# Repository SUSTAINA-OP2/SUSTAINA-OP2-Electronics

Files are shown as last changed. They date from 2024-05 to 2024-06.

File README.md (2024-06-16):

<h1 align="center">
    Printed Circuit Boards for SUSTAINA-OP2&trade;
</h1>
<table align="center">
    <tr>
        <td align="center"><a href="./SUSTAINA-Constant-Voltage-Board">Constant Voltage Board</a></td>
        <td align="center"><a href="./SUTAINA-Control-Switches-Board">Control Switches Board</a></td>
        <td align="center"><a href="./SUSTAINA-PMX-Control-Board">PMX Control Board</a></td>
    </tr>
    <tr>
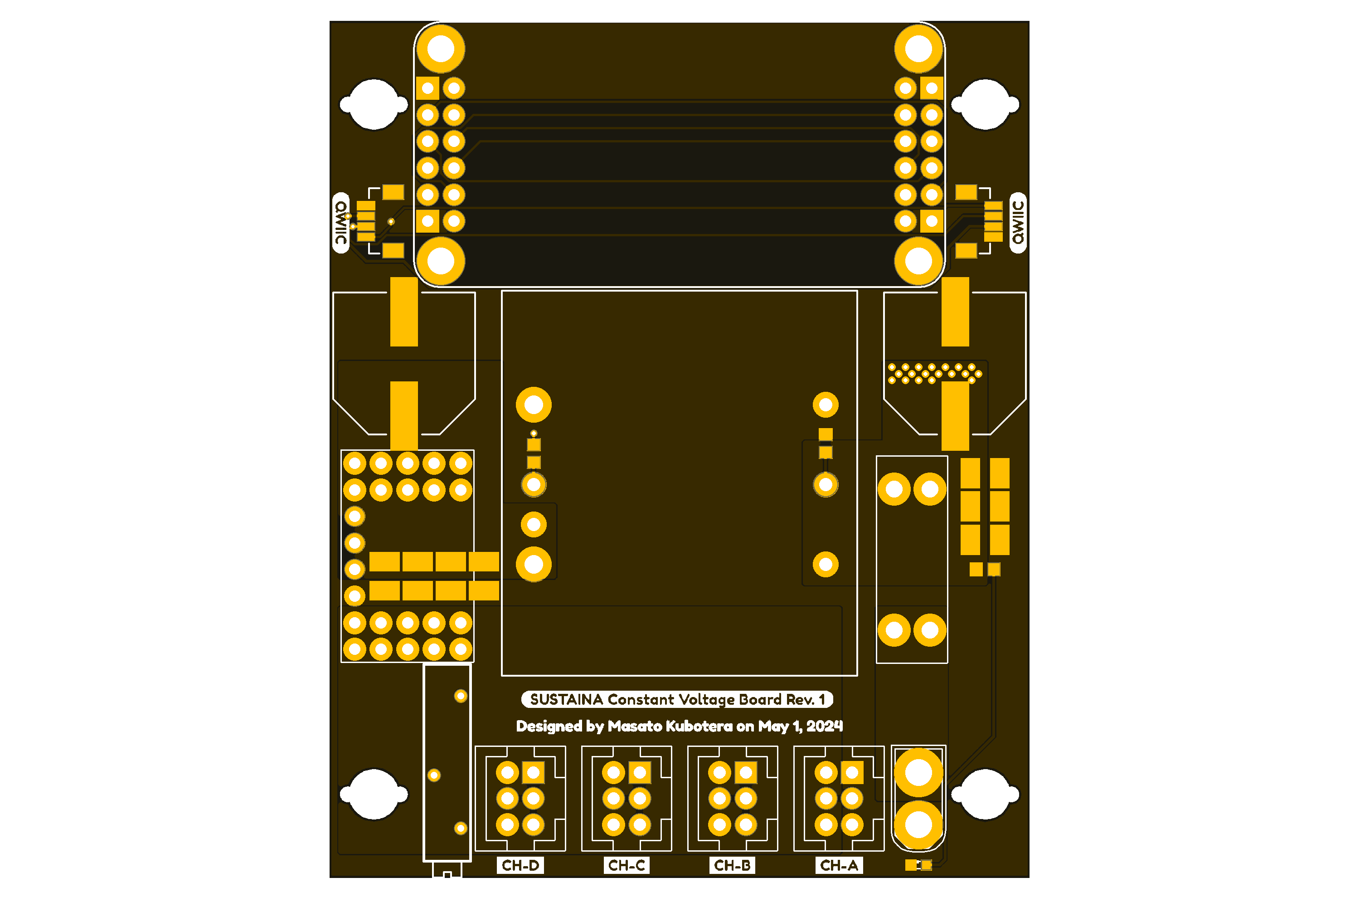
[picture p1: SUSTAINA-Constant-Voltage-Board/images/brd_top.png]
        <td align="center"></td>
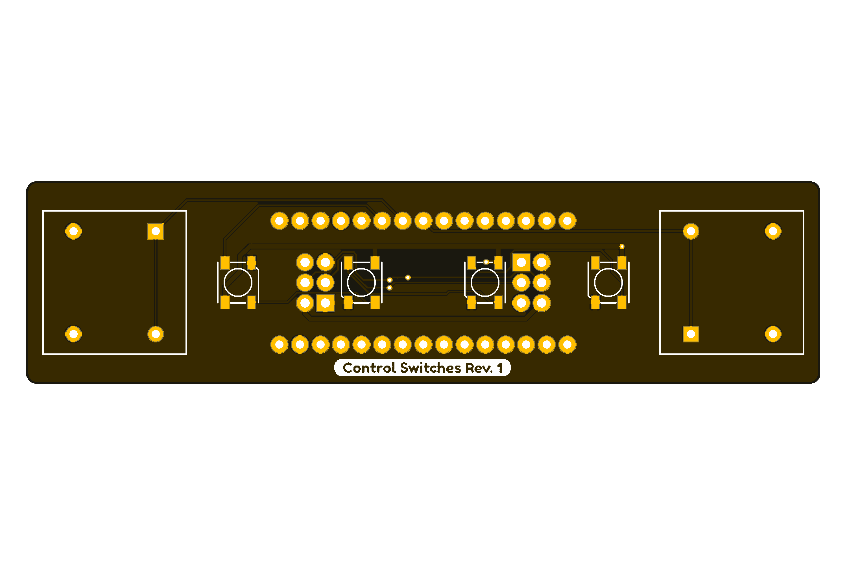
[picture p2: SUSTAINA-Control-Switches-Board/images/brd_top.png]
        <td align="center"></td>
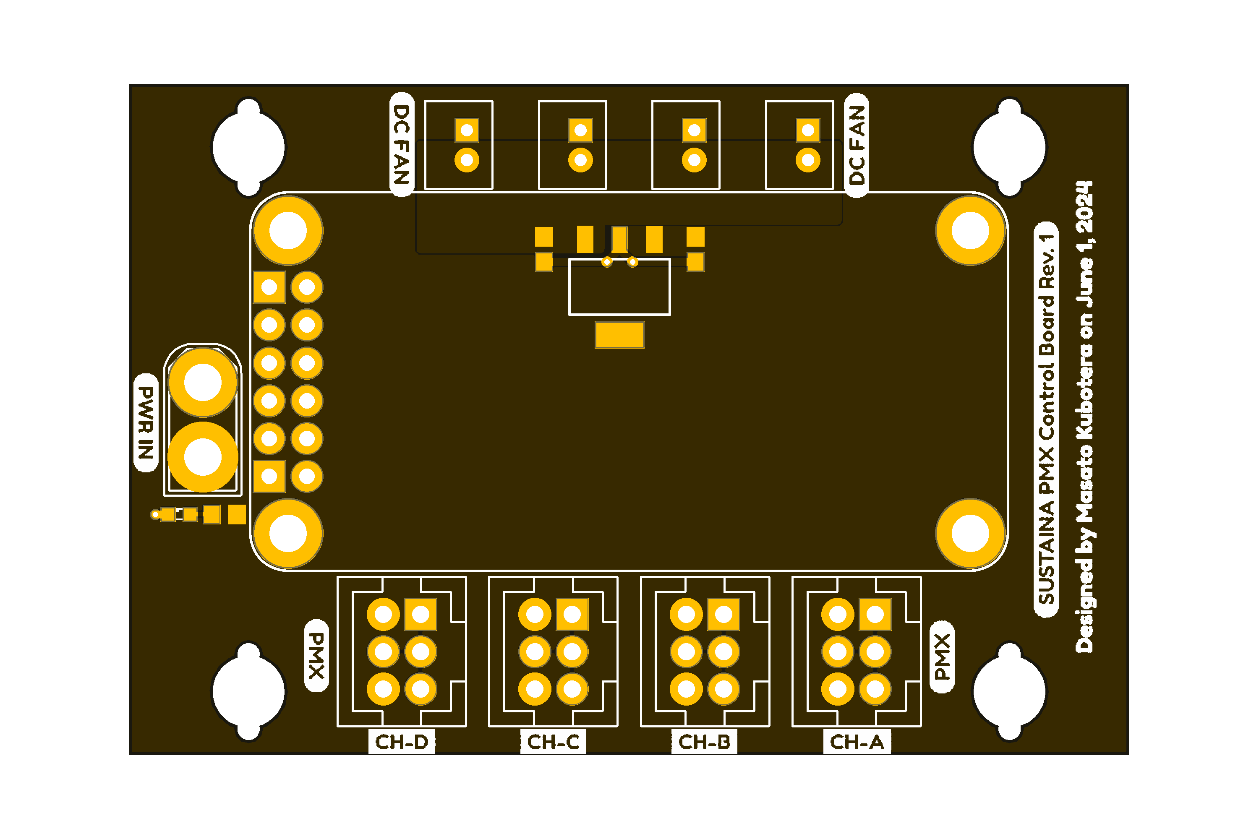
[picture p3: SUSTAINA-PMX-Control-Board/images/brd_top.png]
        <td align="center"></td>
    </tr>
    <tr>
        <td align="center"><a href="./SUSTAINA-Power-Logging-Board">Power Logging Board</a></td>
        <td align="center"><a href="./SUSTAINA-Power-Distribution-Board">Power Distribution Board</a></td>
        <td align="center"><a href="./SUSTAINA-Power-Supply-Switching-Board">Power Supply Switching Board</a></td>
    </tr>
    <tr>
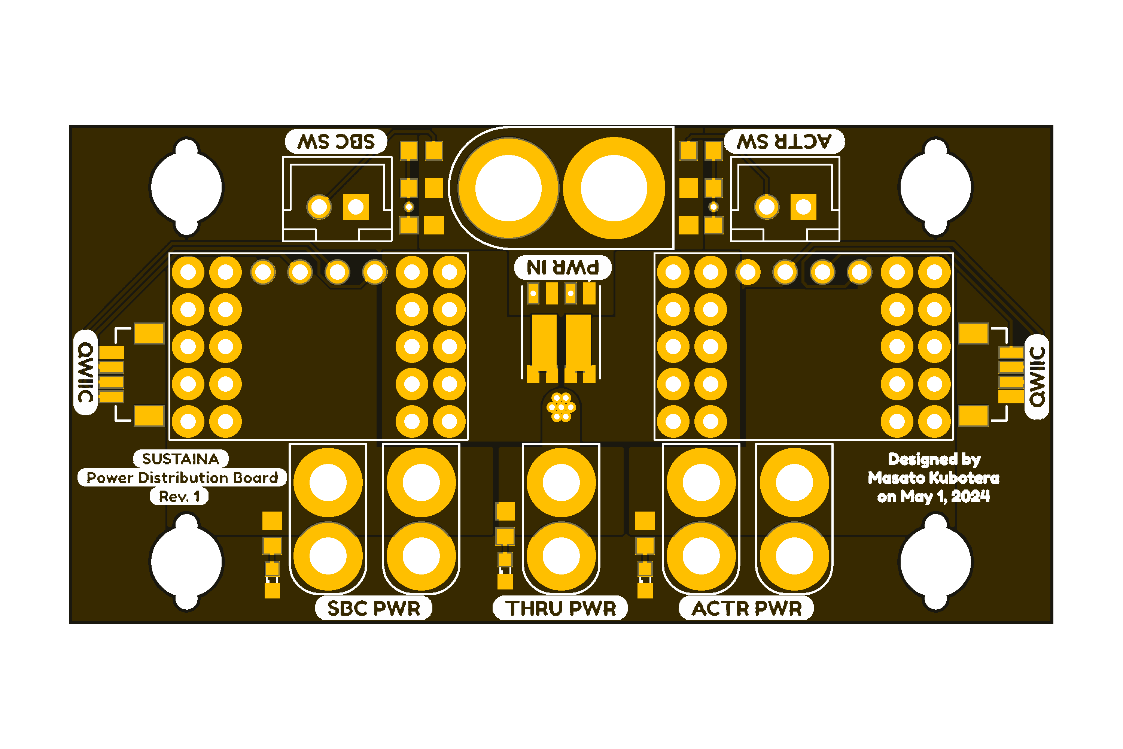
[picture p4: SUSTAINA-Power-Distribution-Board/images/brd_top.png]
        <td align="center"></td>
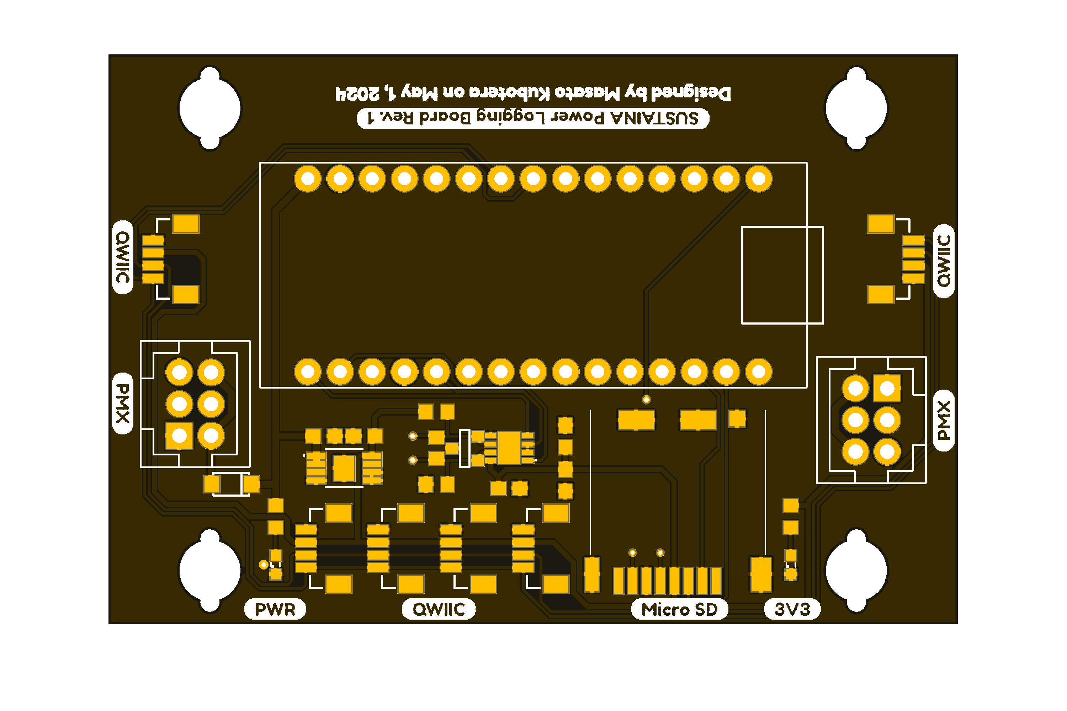
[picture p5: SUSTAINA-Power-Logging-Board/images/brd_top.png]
        <td align="center"></td>
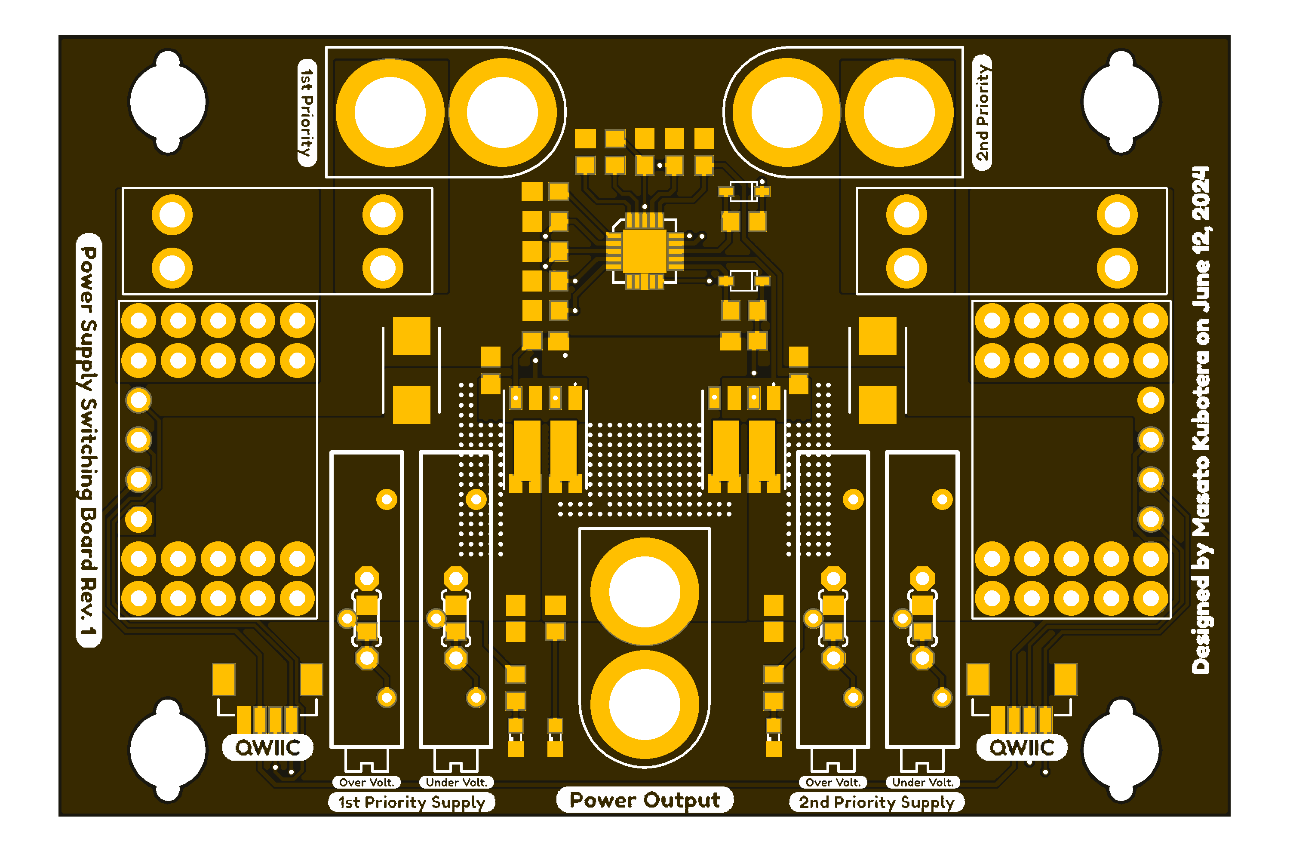
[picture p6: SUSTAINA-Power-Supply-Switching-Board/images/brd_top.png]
        <td align="center"></td>
    </tr>
    <tr>
        <td align="center"><a href="./SUSTAINA-SBC-Power-Board">SBC Power Board</a></td>
        <td align="center"><a href="./SUSTAINA-SCI-Extension-Board">SCI Extension Board</a></td>
        <td align="center"><a href="./SUSTAINA-StrainGauge-Sensing-Board">Strain Gauge Sensing Board</a></td>
    </tr>
    <tr>
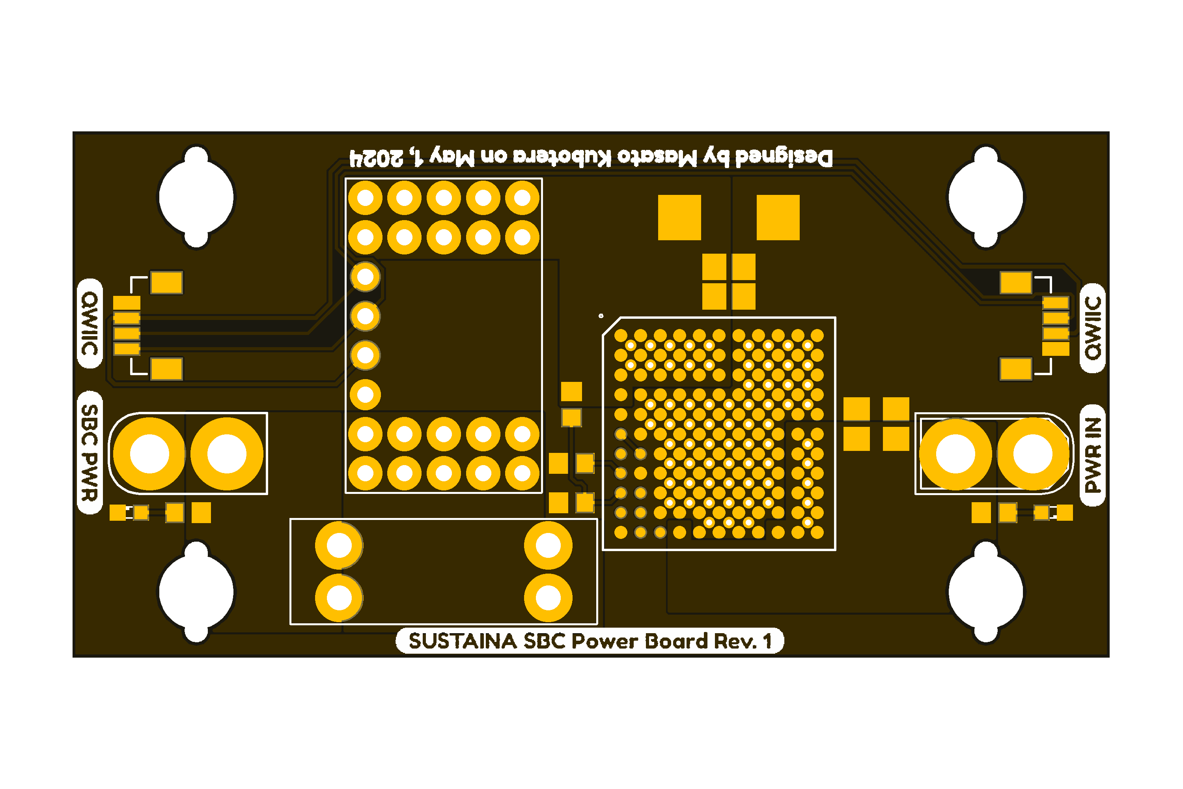
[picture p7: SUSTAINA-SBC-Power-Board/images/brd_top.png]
        <td align="center"></td>
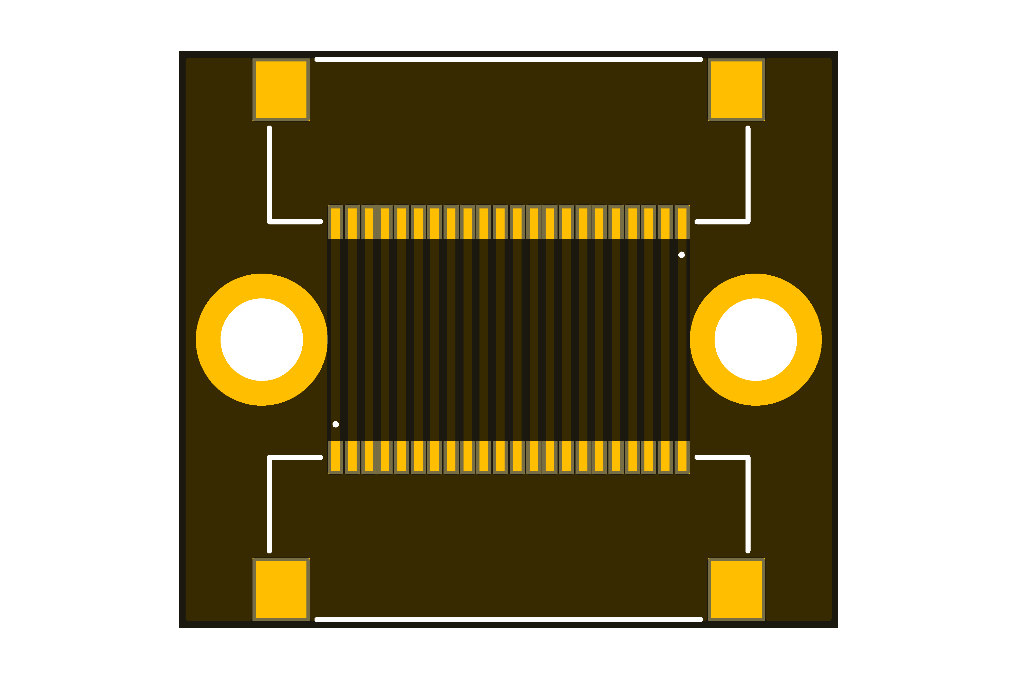
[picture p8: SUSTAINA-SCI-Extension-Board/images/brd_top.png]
        <td align="center"></td>
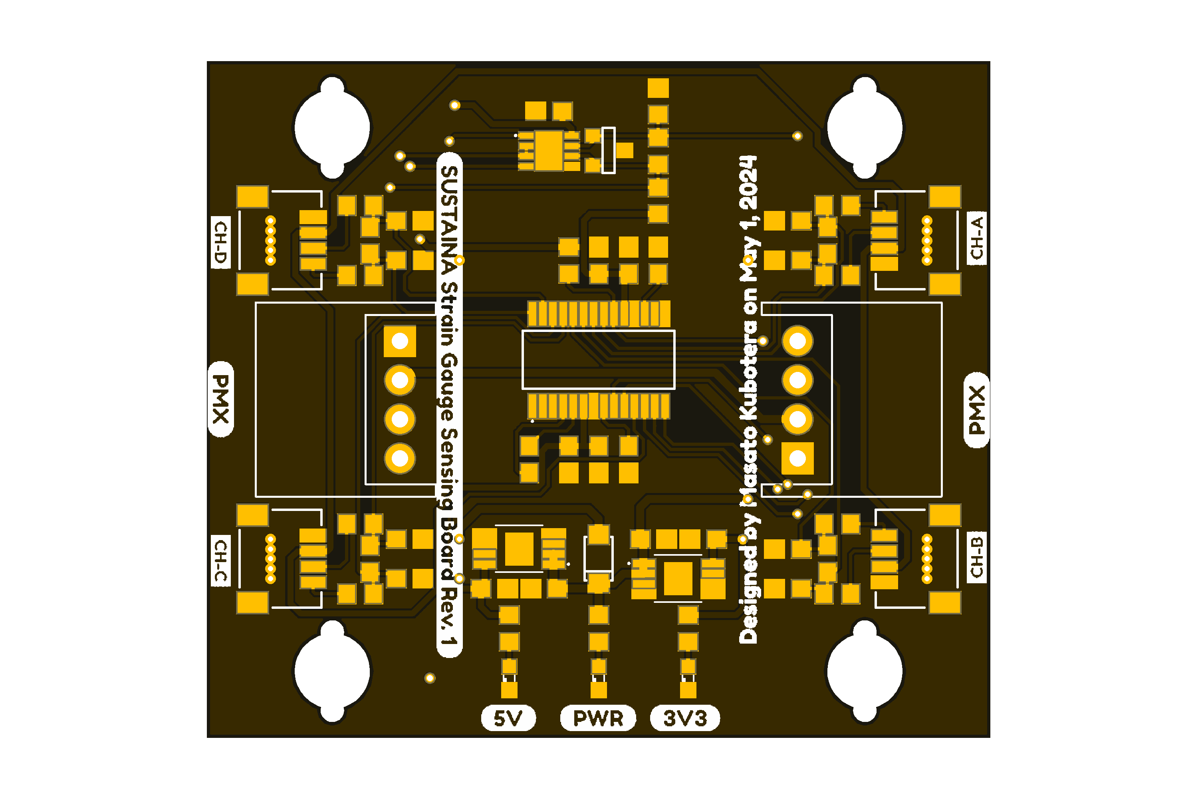
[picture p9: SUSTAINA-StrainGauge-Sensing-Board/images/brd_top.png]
        <td align="center"></td>
    </tr>
    <tr>
        <td align="center"><a href="./SUSTAINA-Power-Monitor-Module">Power Monitor Module</a></td>
        <td align="center"><a href="./SUSTAINA-USB-to-Quad-RS-485-Conv-Module">USB to Quad RS-485 Conv. Module</a></td>
        <td align="center"></td>
    </tr>
    <tr>
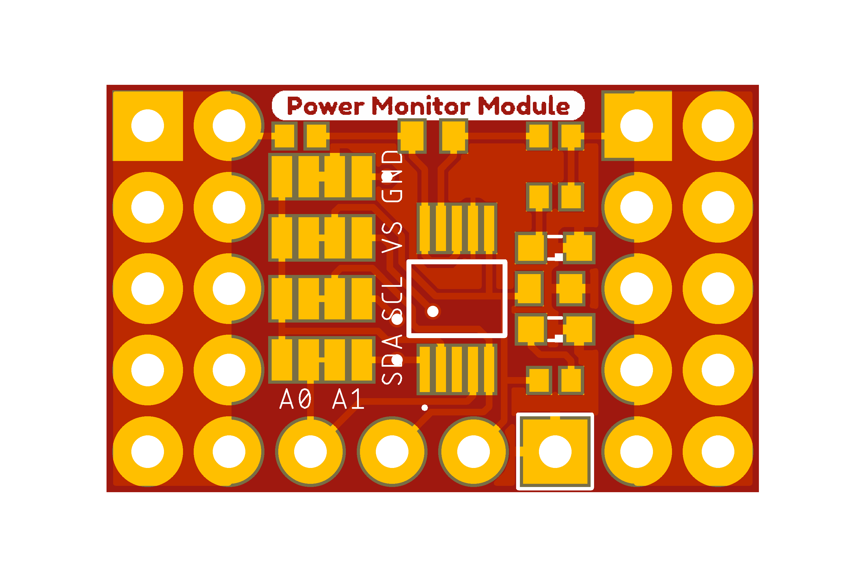
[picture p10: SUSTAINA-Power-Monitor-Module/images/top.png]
        <td align="center"></td>
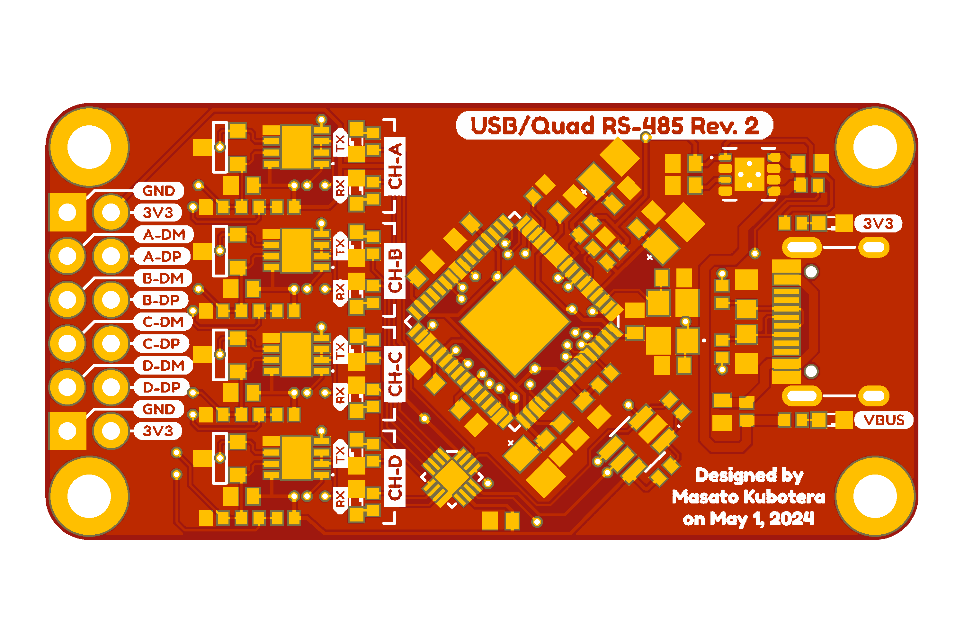
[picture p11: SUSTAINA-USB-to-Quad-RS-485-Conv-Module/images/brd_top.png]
        <td align="center"></td>
        <td align="center"></td>
    </tr>
</table>

> [!NOTE]
> This repository provides design and order data for PCBs of SUSTAINA-OP2&trade;.<br>
> Other SUSTAINA-OP2&trade; contents
> - Mechanical: https://github.com/SUSTAINA-OP/SUSTAINA-OP2
> - Firmware: https://github.com/SUSTAINA-OP/SUSTAINA-OP2-Firmware

## Features of SUSTAINA-OP2&trade;'s PCBs

All PCBs for SUSTAINA-OP are compatible with PCBA, which can reduce production barriers (such as selecting and assembling electronic components) before they are assembled into robots.

The PCB fabrication and PCBA used for all SUSTAINA-OP2 are outsourced to JLCPCB!

> [!WARNING]
> Some components to be assembled on the PCB (e.g. not in stock or not handled)  cannot be assembled using PCBA and must be assembled by yourself.

## Repository Contents

The PCBs of SUSTAINA-OP2&trade; can be divided into two main categories.<br>
The first is "module," which packages sensors, conversion circuits, etc. in functional units on a single board and can be easily replaced.<br>
The second is "board", which is a multifunctional PCB with modules and other components.

### Boards
- [Constant Voltage Board](./SUSTAINA-Constant-Voltage-Board)
- [Control Switches Board](./SUTAINA-Control-Switches-Board)
- [PMX Control Board](./SUSTAINA-PMX-Control-Board)
- [Power Logging Board](./SUSTAINA-Power-Logging-Board)
- [Power Distribution Board](./SUSTAINA-Power-Distribution-Board)
- [Power Supply Switching Board](./SUSTAINA-Power-Supply-Switching-Board)
- [SBC Power Board](./SUSTAINA-SBC-Power-Board)
- [SCI Extension Board](./SUSTAINA-SCI-Extension-Board)
- [StrainGauge Sensing Board](./SUSTAINA-StrainGauge-Sensing-Board)

### Modules
- [Power Monitor Module](./SUSTAINA-Power-Monitor-Module)
- [USB to Quad RS-485 Conv. Module](./SUSTAINA-USB-to-Quad-RS-485-Conv-Module)

## Development Environment
The PCBs for SUSTAINA-OP2&trade; were designed in **Autodesk Eagle 9.6.2**.

## License Information
This product is open source. Please review the [LICENSE(EN)](/LICENSE) / [LICENSE(JA)](/LICENSE-JA) for license information.

This product by Masato Kubotera is licensed under a [CC BY-NC-SA 4.0 DEED](http://creativecommons.org/licenses/by-nc-sa/4.0/).

> [!NOTE]
> **Summary:**
> - **Attribution** — You must give appropriate credit , provide a link to the license, and indicate if changes were made.
> - **NonCommercial** — You may not use the material for commercial purposes.
> - **ShareAlike** — If you remix, transform, or build upon the material, you must distribute your contributions under the same license as the original.

> [!TIP]
> - **Examples of appropriate credit** — [SUSTAINA-OP2&trade;](https://github.com/SUSTAINA-OP/SUSTAINA-OP) &copy; Masato Kubotera (2024) CC BY-NC-SA 4.0 DEED
> >
> - **Reference & Citation**  
>   To reference and/or cite the work contained in this repository, please use the following publications:
>   - Kubotera, M. and Hayashibara, Y.: SUSTAINA-OP&trade;: Kid-sized Open Hardware Platform Humanoid Robot with Emphasis on Sustainability. RoboCup 2023: Robot World Cup XXVI, pp.166–178 (2024) [Springer](https://link.springer.com/chapter/10.1007/978-3-031-55015-7_14)
>
>     **The paper is about SUSTAINA-OP&trade;. Publications on SUSTAINA-OP2&trade; will be published soon.**

## Contact
If you have any questions, please contact the designer of this product, Masato Kubodera, by [E-mail](masatokubotera06@yahoo.co.jp).

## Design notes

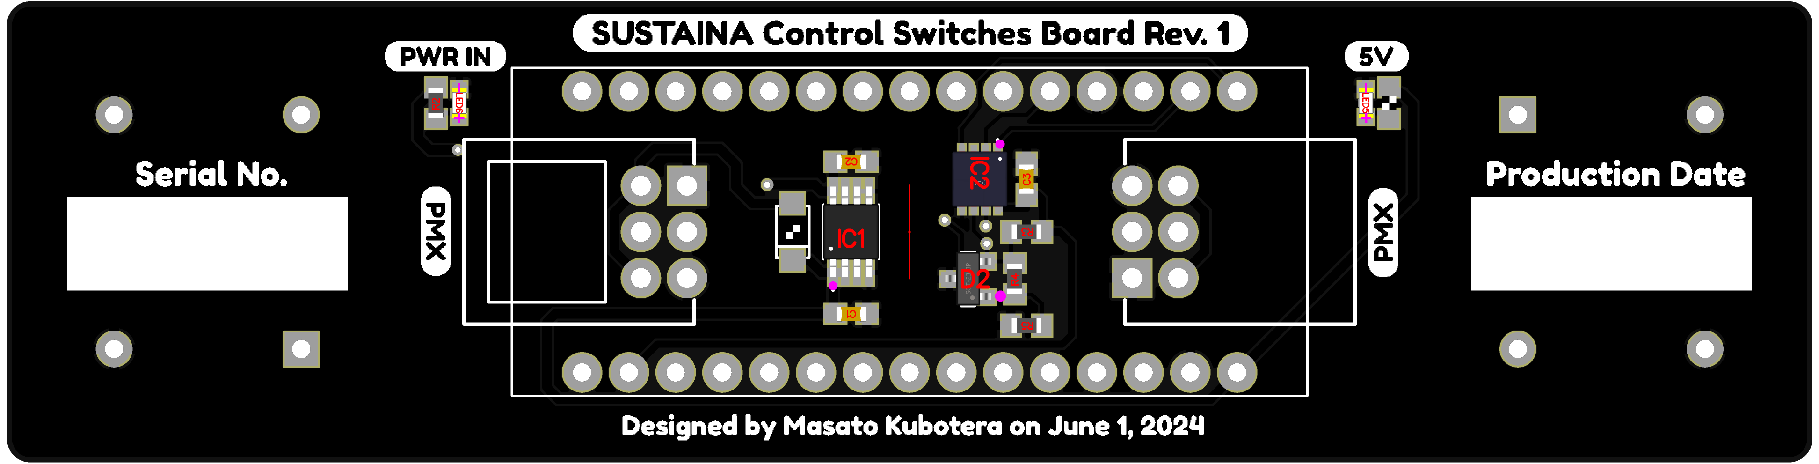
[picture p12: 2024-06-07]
SUSTAINA-Control-Switches-Board/images/pcba_bottom.png

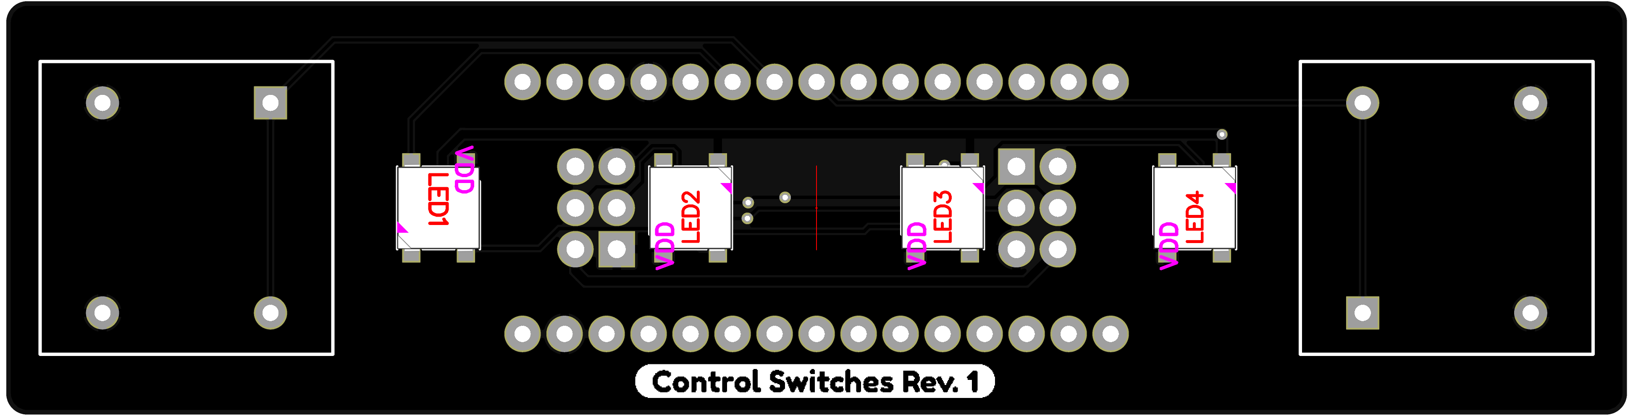
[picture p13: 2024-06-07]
SUSTAINA-Control-Switches-Board/images/pcba_top.png

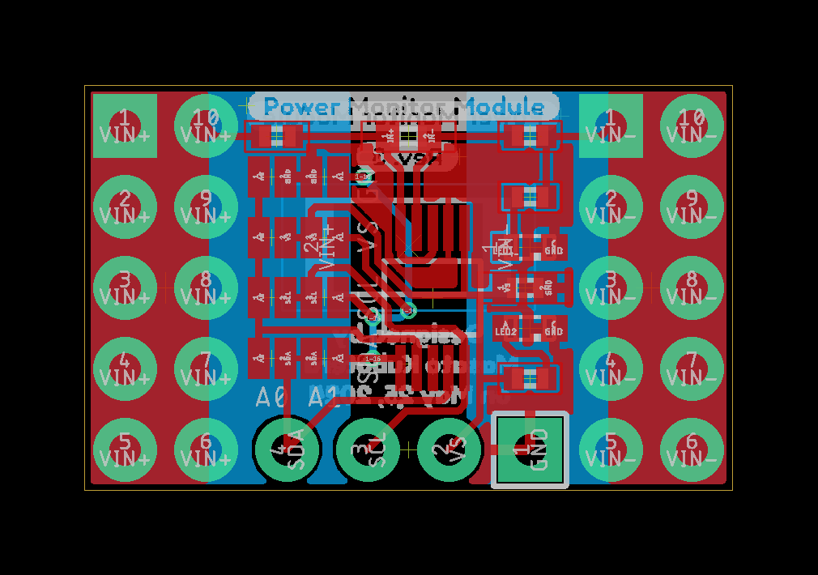
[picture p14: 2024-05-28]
SUSTAINA-Power-Monitor-Module/images/brd.png

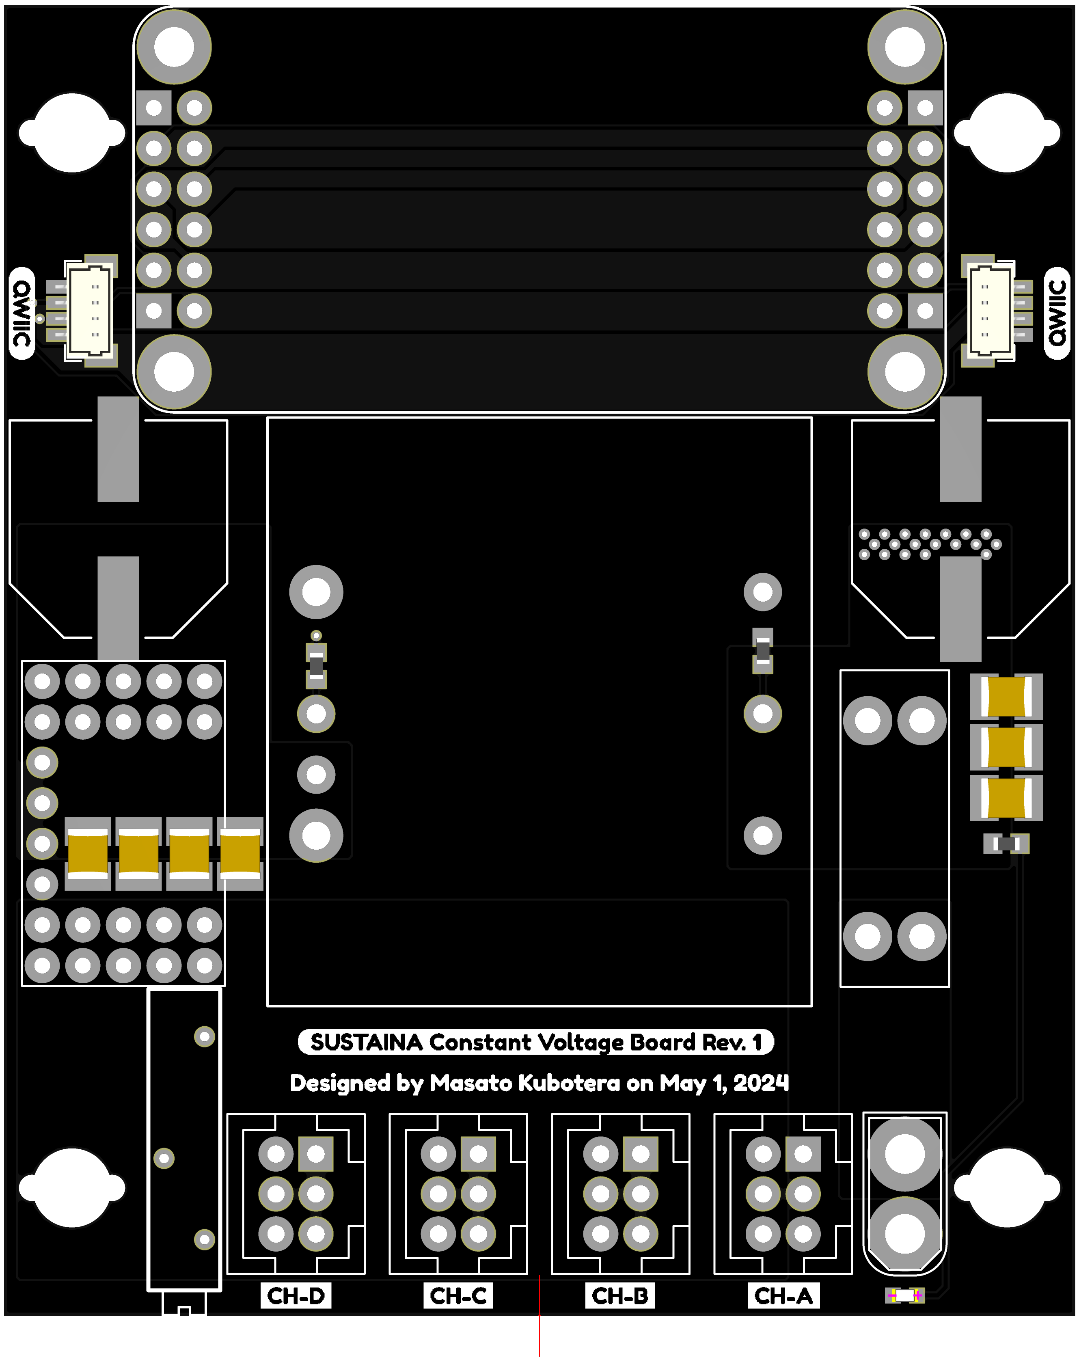
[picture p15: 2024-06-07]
SUSTAINA-Constant-Voltage-Board/images/pcba_top.png

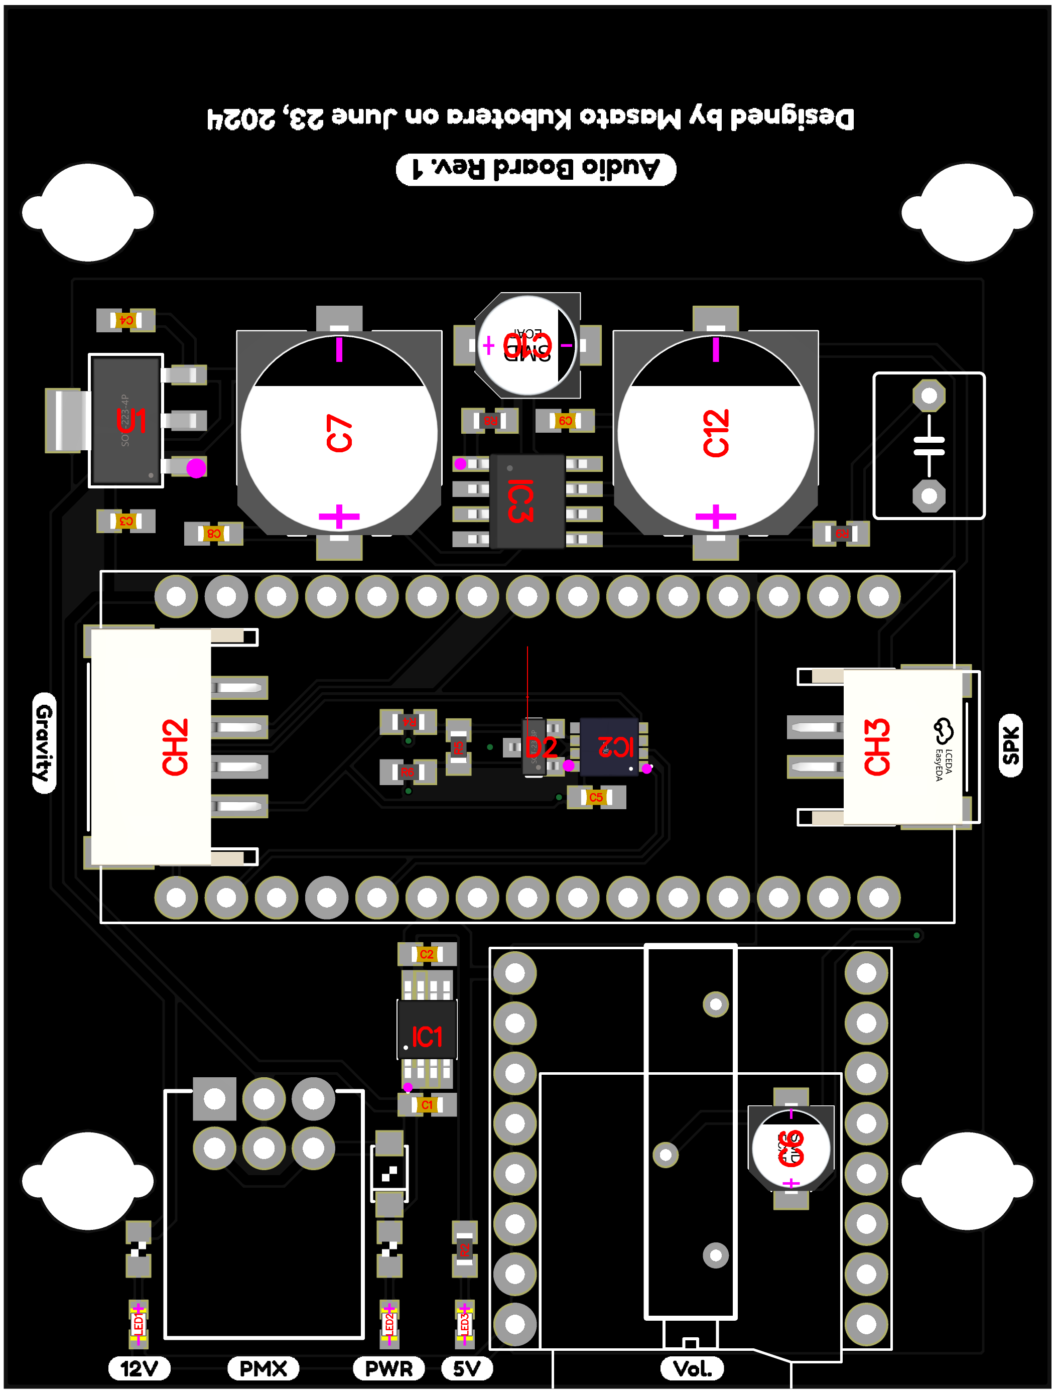
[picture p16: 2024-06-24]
SUSTAINA-Audio-Board/images/pcba.png

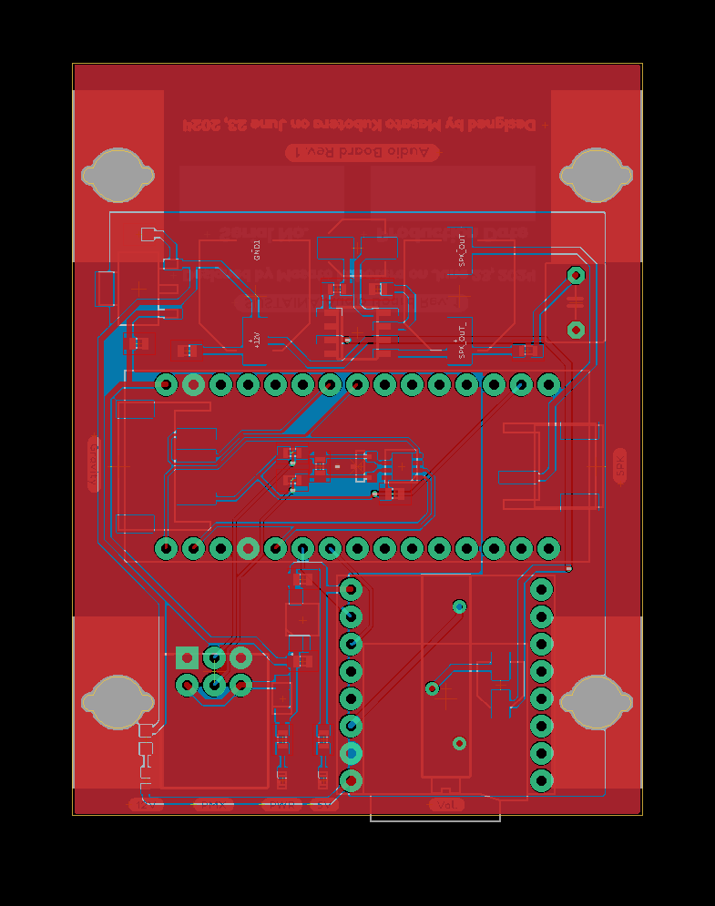
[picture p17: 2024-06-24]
SUSTAINA-Audio-Board/images/brd.png

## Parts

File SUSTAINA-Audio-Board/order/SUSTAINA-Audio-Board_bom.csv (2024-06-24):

Comment | Designator | Footprint | LCSC Part #
10u | C1 C2 C4 | C0603 | C86275
UWT1V100MCL1GB | C10 | UWT1V100MCL1GB | C445058
0.1u | C3 C5 C8 C9 | C0603 | C80516
EEE-1CA4R7NR | C6 | EEE-1CA4R7NR | C401604
UWD1E471MCL1GS | C7 C12 | UWD1E471MCL1GS | C251022
S4B-PH-SM4-TB(LF)(SN) | CH2 | S4B-PH-SM4-TB(LF)(SN) | C265102
S2B-PH-SM4-TB(LF)(SN) | CH3 | S2B-PH-SM4-TB(LF)(SN) | C295747
SS34FA | D1 | SS34FA | C719833
CDSOT23-SM712 | D2 | CDSOT23-SM712 | C404012
TPS7B82-Q1 | IC1 | SOP65P490X110-9N | C424924
SN65HVD75DRBR | IC2 | SON65P300X300X100-9N | C98708
LM386M-1 | IC3 | SO08 | C5375298
Green | LED1 LED2 LED3 | SML0603 | C2922668
2k | R1 R3 | R0603 | C2097078
1k | R2 | R0603 | C22548
680 | R4 R6 | R0603 | C112310
120 | R5 | R0603 | C114640
180 | R8 | R0603 | C137786
10 | R9 | R0603 | C109318
LM2937IMP-12NOPB | U1 | SOT-223 | C5220609

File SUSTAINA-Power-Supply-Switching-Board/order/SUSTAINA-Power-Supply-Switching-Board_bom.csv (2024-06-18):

Comment | Designator | Footprint | LCSC Part #
0 | R7 R8 | R0603 | C100044
0.1u | C1 C2 C4 C6 C8 | C0603 | C2929177
1n | C3 | C0603 | C153291
1u | C5 C7 C9 C10 | C0603 | C86020
2k | R1 R2 R11 R21 R22 | R0603 | C2097078
10k | R9 R10 | R0603 | C98220
100 | R3 R4 R5 R6 | R0603 | C105588
680 | R20 R23 | R0603 | C112310
BAT54J 115 | D1 | SOD-323-2 | C130415
BAT54J 115 | D2 | SOD-323-2 | C130415
BM04B-SRSS-TB | CH3 CH5 | BM04B-SRSS-TB | C160390
Green | LED1 LED2 LED3 | SML0603 | C2922668
LTC4418IUF | IC1 | LTC4418IUF | C580908
SI7997DP-T1-GE3 | U1 U2 | POWERPAK_SO-8_VIS | C913432
SMBJ30CA | D3 D4 | SMBJ30CA | C83847

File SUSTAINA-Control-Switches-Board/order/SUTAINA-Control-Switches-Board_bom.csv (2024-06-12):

Comment | Designator | Footprint | LCSC Part #
CDSOT23-SM712 | D2 | CDSOT23-SM712 | C404012
Green | LED5 LED6 | SML0603 | C2922668
0.1u | C3 | C0402 | C80516
1k | R2 | R0603 | C22548
2k | R1 | R0603 | C2097078
10u | C1 C2 | C0603 | C86275
120 | R4 | R0603 | C114640
680 | R3 R5 | R0603 | C112310
SN65HVD75DRBR | IC2 | SON65P300X300X100-9N | C98708
SS34FA | D1 | SS34FA | C719833
TPS7B82-Q1 | IC1 | SOP65P490X110-9N | C424924
WS2812B | LED1 LED2 LED3 LED4 | WS2812B | C2874885

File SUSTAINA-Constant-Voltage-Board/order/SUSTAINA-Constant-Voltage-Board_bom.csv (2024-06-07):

Comment | Designator | Footprint | LCSC Part #
0 | R2 | R0603 | C100044
2k | R1 | R0603 | C105576
10u | C2 C3 C4 C5 C6 C7 C8 | C1210 | C77102
100 | R3 | R0603 | C105588
BM04B-SRSS-TB | CH6 CH7 | BM04B-SRSS-TB | C160390
Green | LED1 | SML0603 | C510025
UCM1J361MNJ1MS | C1 C9 | UCM1J361MNJ1MS | C3829716

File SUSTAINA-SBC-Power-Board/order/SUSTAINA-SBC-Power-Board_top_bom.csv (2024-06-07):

Comment | Designator | Footprint | LCSC Part #
2k | R1 R5 | R0603 | C2097078
4.7u | C1 C2 | C0805 | C98192
6.98k | R4 | R0603 | C137686
22u | C3 C5 | C0805 | C86816
45.3k | R2 | R0603 | C245971
47u | C6 | D/7343-31R | C1955280
100k | R3 | R0603 | C14675
BM04B-SRSS-TB | CH3 CH4 | BM04B-SRSS-TB | C160390
Green | LED1 LED3 | SML0603 | C2922668
LTM8055 | IC1 | LTM8055 | C690729

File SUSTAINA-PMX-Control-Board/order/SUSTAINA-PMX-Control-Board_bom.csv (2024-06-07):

Comment | Designator | Footprint | LCSC Part #
0.1u | C1 | C0603 | C2929177
2k | R1 | R0603 | C2097078
10u | C2 | C0603 | C86275
Green | LED1 | SML0603 | C2922668
LM2937IMP-12NOPB | U1 | SOT-223 | C5220609

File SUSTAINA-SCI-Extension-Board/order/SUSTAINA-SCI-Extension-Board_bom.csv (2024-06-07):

Comment | Designator | Footprint | LCSC Part #
XF2M-2215-1A | CH1 CH2 | XF2M-2215-1A | C231416

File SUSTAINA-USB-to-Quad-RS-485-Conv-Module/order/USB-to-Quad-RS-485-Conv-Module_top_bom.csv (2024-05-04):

Comment | Designator | Footprint | LCSC Part #
7V12006001 | CR1 | 7V12006001 | C5203634
0.01u | C1 C3 | C0402 | C272878
30p | C19 C20 | C0402 | C277479
1u | C2 | C0402 | C115046
2.2u | C4 | C0402 | C2997286
4.7u | C5 C7 C16 | 0805K | C516051
0.1u | C6 C8 C9 C10 C11 C12 C13 C14 C15 C17 C18 C21 C22 C23 C24 C25 | C0402 | C541464
PGB1010603MR | D1 D2 | 603 | C142698
CDSOT23-SM712 | D3 D4 D5 D6 | SOT-23-3 | C404012
BLM15AX601SN1D | FL1 FL2 FL3 | BLM15AX601SN1D | C76886
FT4232HQ | IC1 | FT4232HQ | C2651882
93LC56BT-I/OT | IC2 | SOT-23-6 | C190271
SN65HVD75DRBR | IC3 IC4 IC5 IC6 | SON65P300X300X100-9N | C98708
SN74HC595B | IC7 | QFN40P250X250X50-17N | C2682068
Green | LED1 LED2 LED8 LED10 LED12 LED14 | SML0603 | C2922668
Red | LED7 LED9 LED11 LED13 | SML0603 | C253533
470 | R1 R2 R22 R23 R24 R25 R26 R27 R28 R29 | R0402 | C114877
680 | R10 R12 R13 R15 R16 R18 R19 R21 | R0402 | C137948
120 | R11 R14 R17 R20 | R0402 | C114758
10 | R3 R4 | R0402 | C138066
15k | R5 | R0402 | C11476
10k | R6 R8 R30 | R0402 | C60490
12k | R7 | R0402 | C114760
2k | R9 | R0402 | C60488
TPS73533DRBT | U1 | SON-8 | C115872
USB-C-2.0 | USB1 | USB-C-2.0 | C2927300

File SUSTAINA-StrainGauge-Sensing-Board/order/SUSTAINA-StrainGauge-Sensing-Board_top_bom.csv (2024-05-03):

Comment | Designator | Footprint | LCSC Part #
CDSOT23-SM712 | D2 | CDSOT23-SM712 | C404012
0.1u | C5 C19 C24 | C0603 | C80516
1k | R2 R3 R7 R8 R9 R10 R11 R12 R13 R14 R15 | R0603 | C22548
1n | C6 C7 C8 C9 C10 C11 C12 C13 C14 C15 C16 C17 | C0603 | C153291
1u | C18 C20 C21 C23 | C0603 | C431003
2k | R1 | R0603 | C105576
4.7n | C22 | C0603 | C2180681
10u | C1 C2 C3 C4 | C0603 | C86275
120 | R5 | R0603 | C114640
680 | R4 R6 | R0603 | C112310
ADS1262 | IC4 | SOP65P640X120-28N | C2669963
Green | LED1 LED2 LED3 | SML0603 | C2922668
SM04B-SRSS-TB | CH1 CH2 CH3 CH4 | SM04B-SRSS-TB | C160404
SN65HVD75DRBR | IC3 | SON65P300X300X100-9N | C98708
SS34FA | D1 | SS34FA | C719833
TPS7B82-Q1 | IC1 | SOP65P490X110-9N | C5220182
TPS7B82-Q1 | IC2 | SOP65P490X110-9N | C424924

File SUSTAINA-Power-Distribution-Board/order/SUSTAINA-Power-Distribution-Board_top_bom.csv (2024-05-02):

Comment | Designator | Footprint | LCSC Part #
0.1u | C1 C2 | C0603
2k | R5 R6 R7 | R0603
10k | R1 R2 R3 R4 | R0603
BM04B-SRSS-TB | CH9 CH10 | BM04B-SRSS-TB
Green | LED1 LED2 LED3 | SML0603
SI7997DP-T1-GE3 | U1 | POWERPAK_SO-8_VIS

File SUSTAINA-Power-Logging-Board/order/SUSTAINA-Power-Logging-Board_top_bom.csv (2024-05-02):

Comment | Designator | Footprint | LCSC Part #
0.1u | C3 C4 C5 | C0603 | C80516
1k | R2 | R0603 | C22548
2k | R1 | R0603 | C105576
10u | C1 C2 | C0603 | C86275
120 | R4 | R0603 | C114640
680 | R3 R5 | R0603 | C112310
BM04B-SRSS-TB | CH2 CH3 CH4 CH5 CH6 CH7 | BM04B-SRSS-TB | C160390
DM3CS-SF | CH1 | DM3CS-SF | C202111
Green | LED1 LED2 | SML0603 | C2922668
SN65HVD75DRBR | IC2 | SON65P300X300X100-9N | C98708
SS34FA | D1 | SS34FA | C719833
TPS7B82-Q1 | IC1 | SOP65P490X110-9N | C5220182
CDSOT23-SM712 | D2 | CDSOT23-SM712 | C404012

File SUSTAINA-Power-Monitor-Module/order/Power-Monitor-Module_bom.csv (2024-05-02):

Comment | Designator | Footprint | LCSC Part #
0.1u | C1 C2 | C0402 | C541464
2k | R4 R5 | R0402 | C106235
4.7 | R2 R3 | R0402 | C137962
INA226 | IC1 | MSOP-10 | C49851
Red | LED1 | SML0603 | C510027
SHORTLAND | JP1 JP2 JP3 JP4 JP5 JP6 JP7 JP8 | SHORTLAND
Yellow | LED2 | SML0603 | C510025
0.002 | R1 | R2512 | C2838967

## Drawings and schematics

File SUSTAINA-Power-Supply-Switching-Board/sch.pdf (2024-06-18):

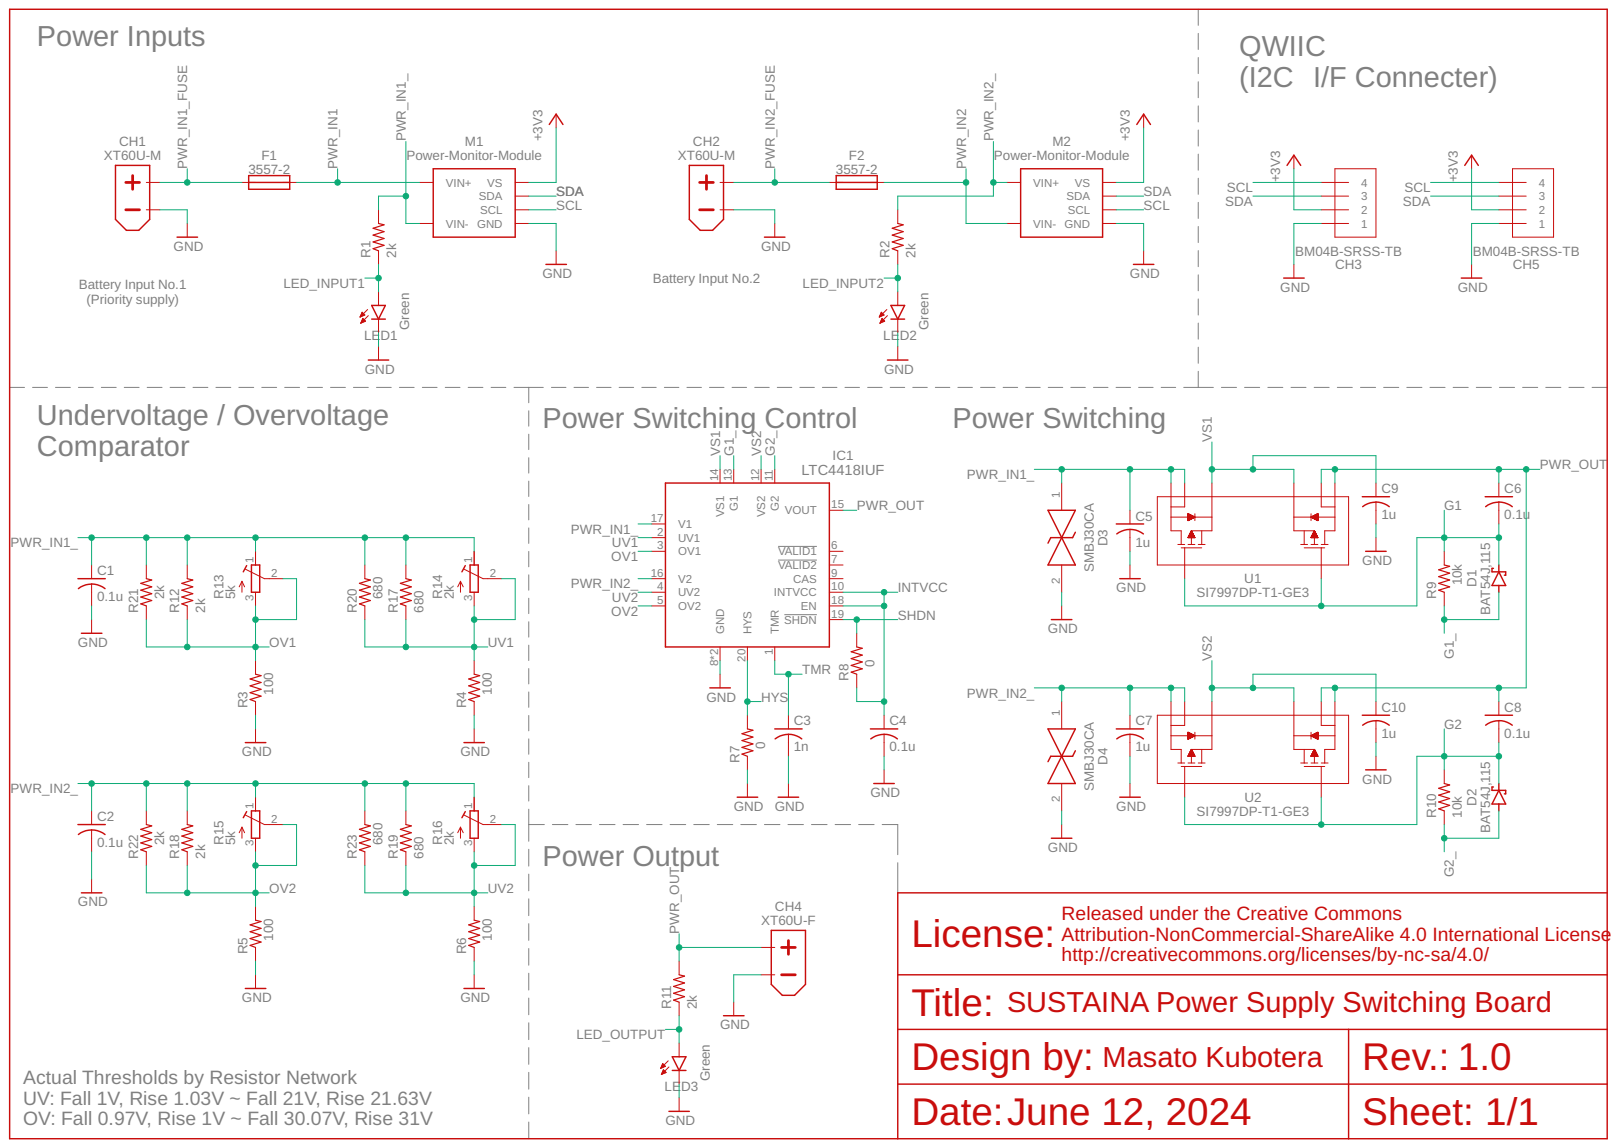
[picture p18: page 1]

Released under the Creative Commons
Attribution-NonCommercial-ShareAlike 4.0 International License

http://creativecommons.org/licenses/by-nc-sa/4.0/ License:
Title:

SUSTAINA Power Supply Switching Board

Design by: Masato Kubotera | Rev.: 1.0
Date: June 12, 2024 | Sheet: 1/1

Actual Thresholds by Resistor Network
UV: Fall 1V, Rise 1.03V ~ Fall 21V, Rise 21.63V
OV: Fall 0.97V, Rise 1V ~ Fall 30.07V, Rise 31V

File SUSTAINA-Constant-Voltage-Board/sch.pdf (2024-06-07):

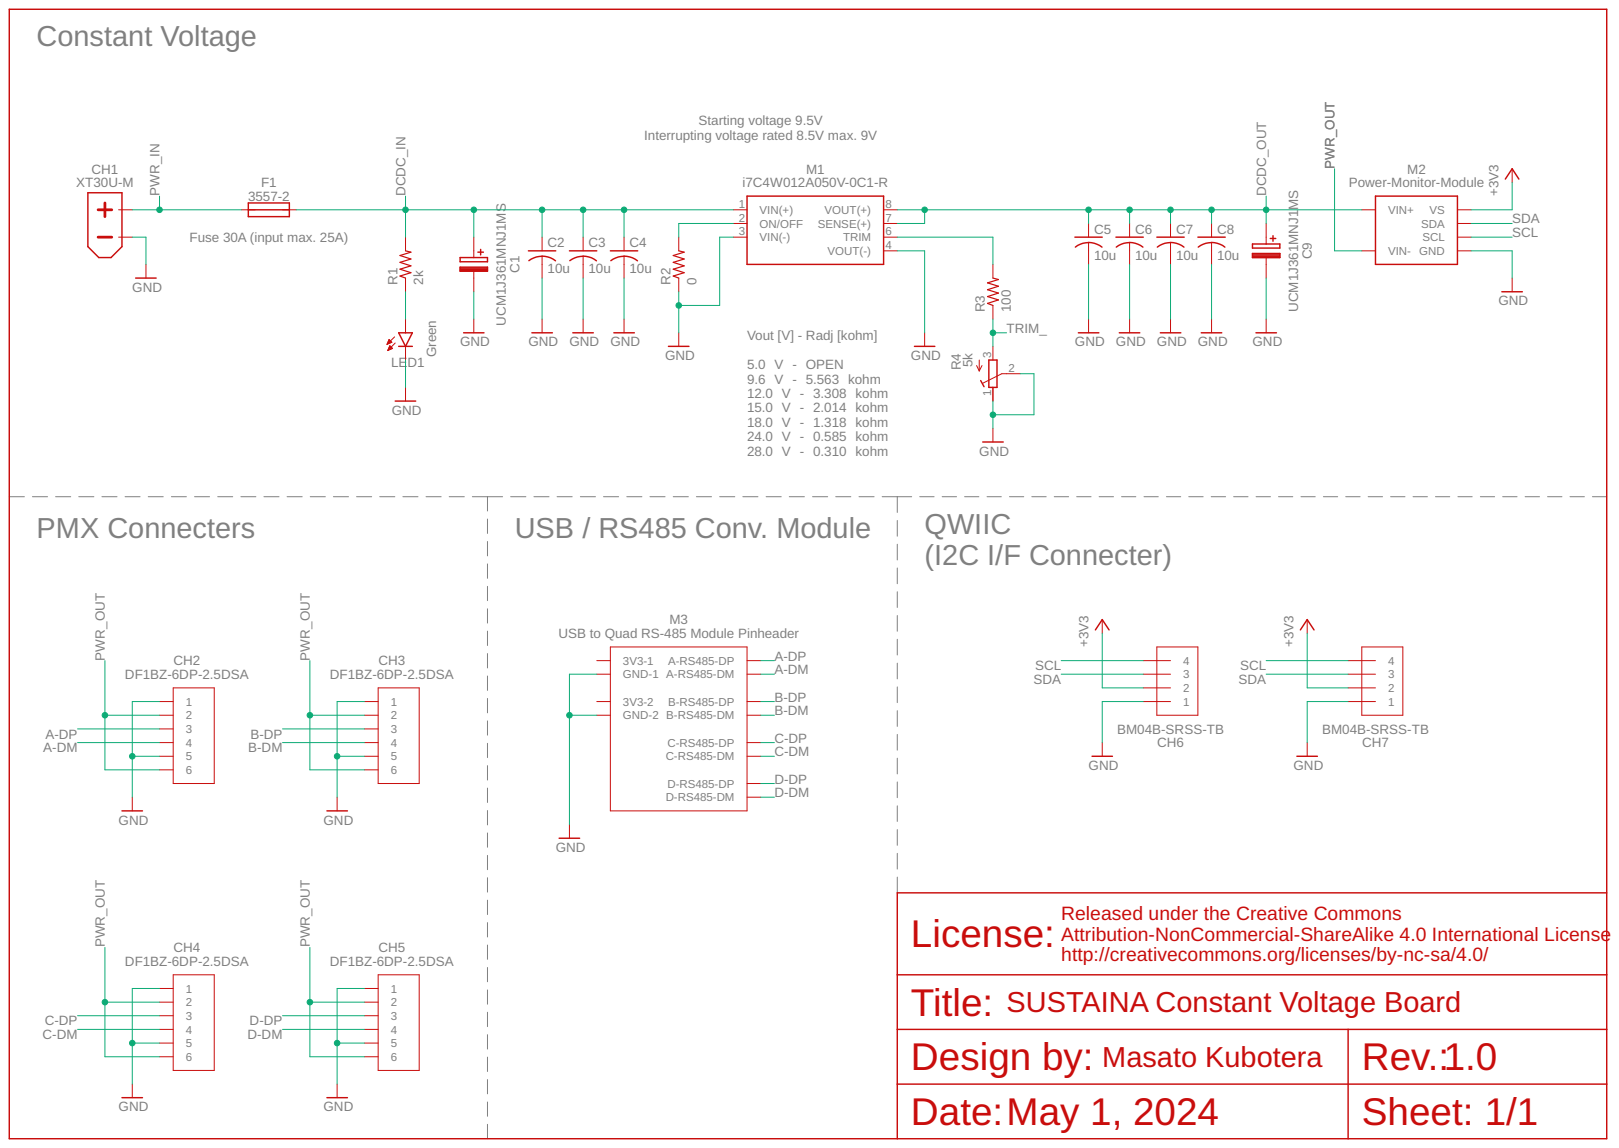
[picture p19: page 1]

Interrupting voltage rated 8.5V max. 9V

USB to Quad RS-485 Module Pinheader

Released under the Creative Commons
Attribution-NonCommercial-ShareAlike 4.0 International License

http://creativecommons.org/licenses/by-nc-sa/4.0/ License:
Title:

SUSTAINA Constant Voltage Board

Design by: Masato Kubotera | Rev.: 1.0
Date: | Sheet: 1/1

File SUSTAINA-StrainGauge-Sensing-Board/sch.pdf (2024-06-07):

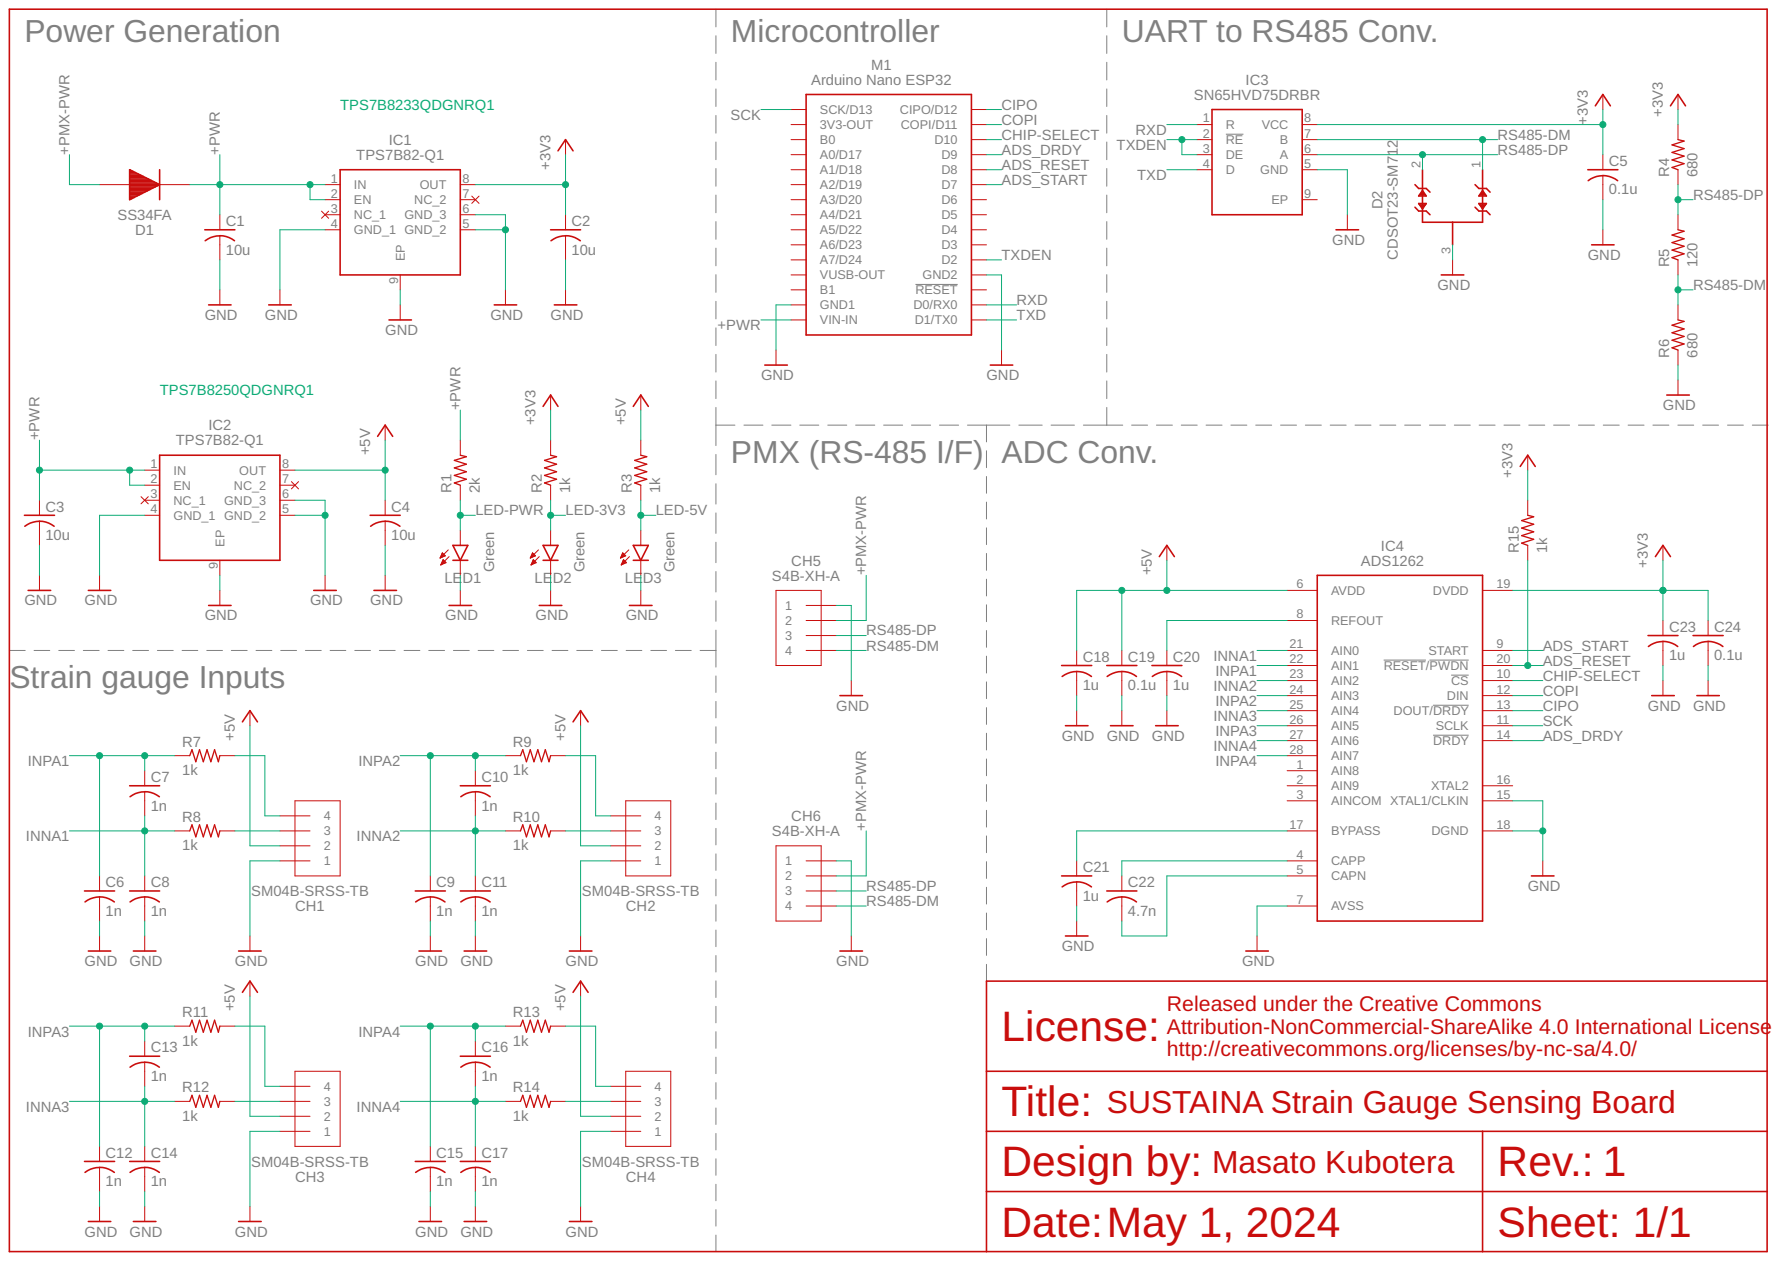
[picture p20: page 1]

D1/TX0 D0/RX0 RESET GND2 D2 D3 D4 D5 D6 D7 D8 D9 D10 COPI/D11 CIPO/D12 M1
3V3-OUT A0/D17 A1/D18 A2/D19 A3/D20 A4/D21 A5/D22 A6/D23 A7/D24 VUSB-OUT B1GND1 VIN-IN

+PMX-PWR

Released under the Creative Commons
Attribution-NonCommercial-ShareAlike 4.0 International License

http://creativecommons.org/licenses/by-nc-sa/4.0/ License:
Title:
Design by:
Date:

SUSTAINA Strain Gauge Sensing Board

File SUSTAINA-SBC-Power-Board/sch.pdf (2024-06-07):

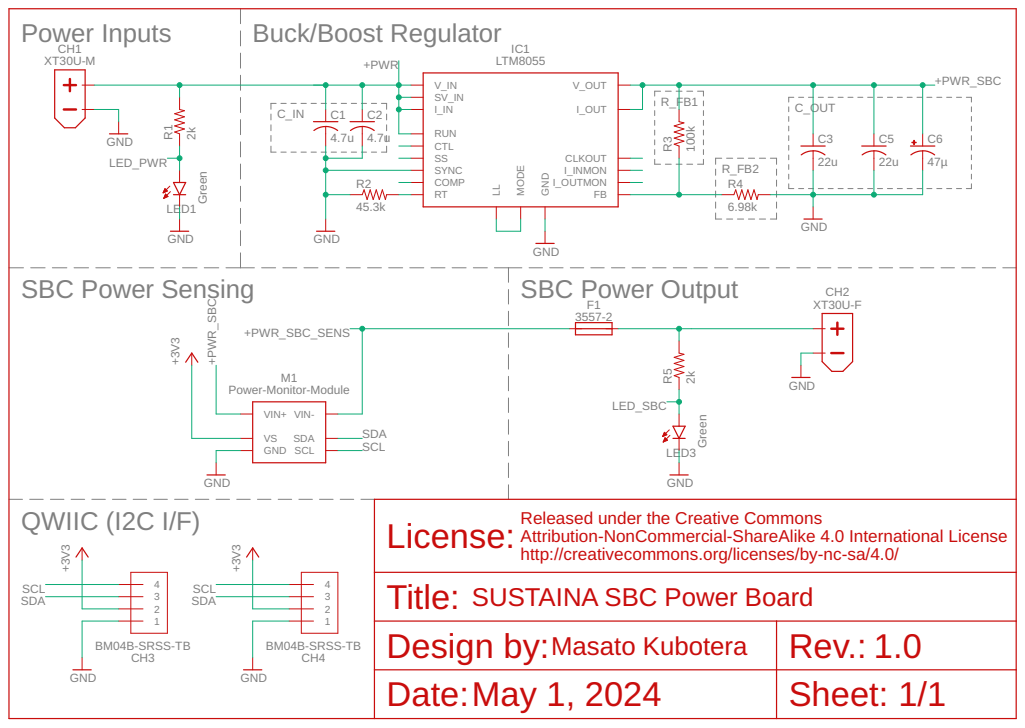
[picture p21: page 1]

Released under the Creative Commons
Attribution-NonCommercial-ShareAlike 4.0 International License

http://creativecommons.org/licenses/by-nc-sa/4.0/ License:

SUSTAINA SBC Power Board

Design by: Masato Kubotera | Rev.: 1.0
Date: May 1, 2024 | Sheet: 1/1

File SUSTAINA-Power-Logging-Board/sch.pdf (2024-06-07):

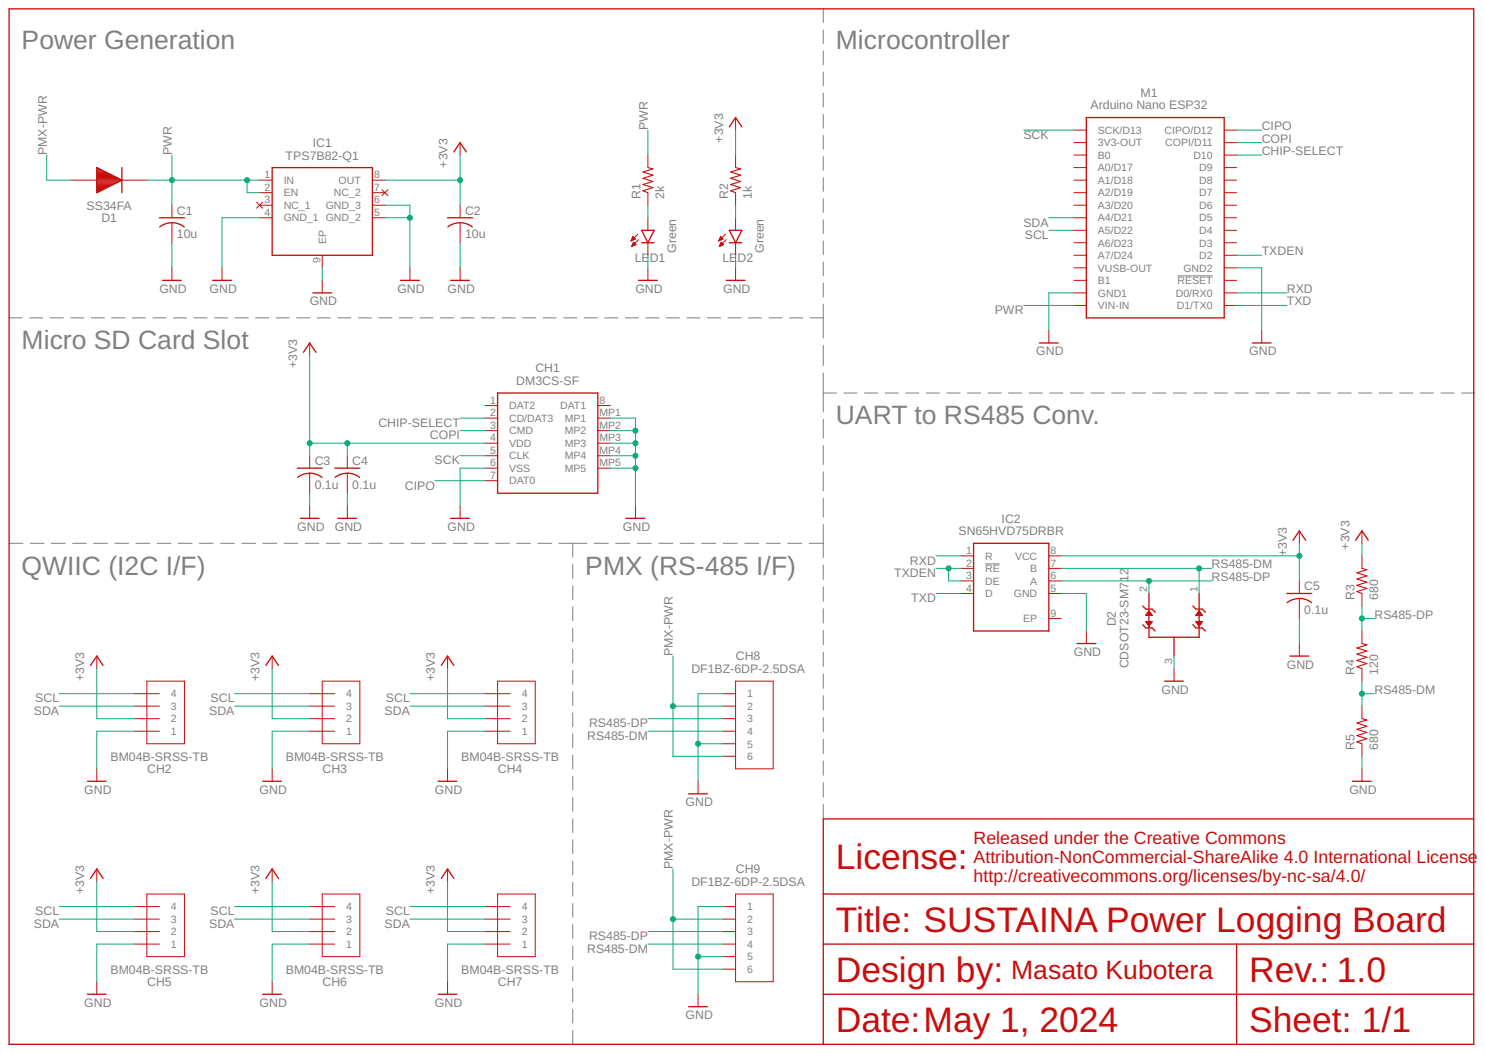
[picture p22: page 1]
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

UART to RS485 Conv. Micro SD Card Slot

PMX-PWR

Released under the Creative Commons
Attribution-NonCommercial-ShareAlike 4.0 International License
SUSTAINA Power Logging Board

http://creativecommons.org/licenses/by-nc-sa/4.0/ License:
Title:

Design by: Masato Kubotera | Rev.: 1.0
Date: May 1, 2024 | Sheet: 1/1

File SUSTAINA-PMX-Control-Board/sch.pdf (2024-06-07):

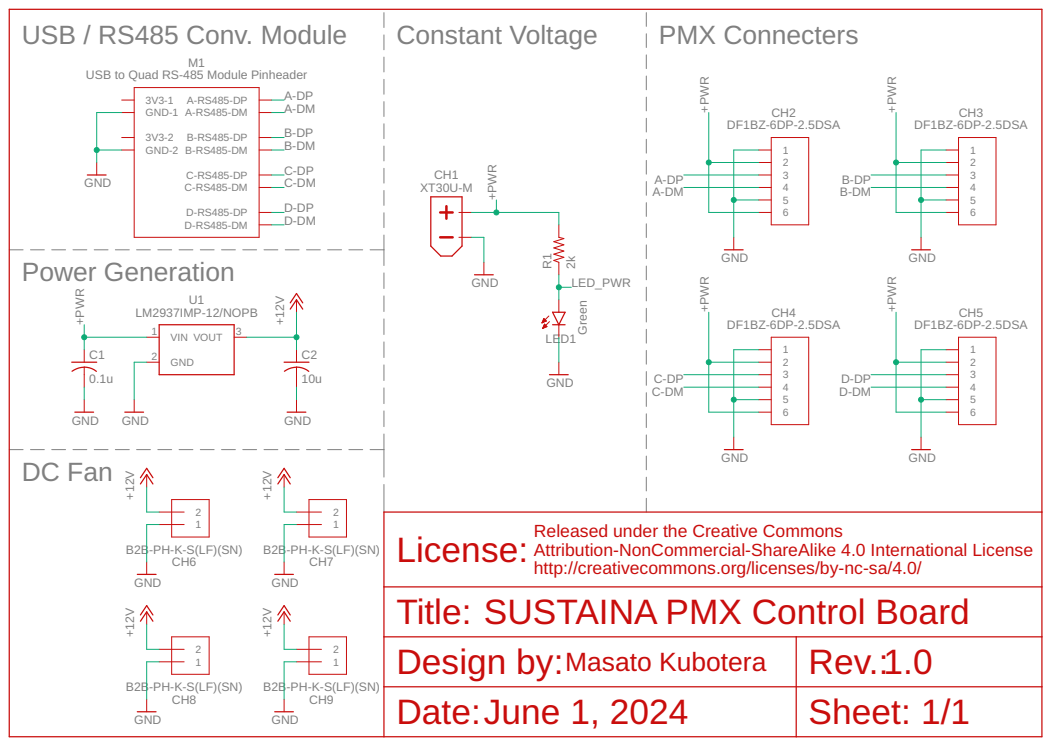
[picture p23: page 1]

USB to Quad RS-485 Module Pinheader

Released under the Creative Commons
Attribution-NonCommercial-ShareAlike 4.0 International License
SUSTAINA PMX Control Board
Design by:
June 1, 2024

http://creativecommons.org/licenses/by-nc-sa/4.0/ License:

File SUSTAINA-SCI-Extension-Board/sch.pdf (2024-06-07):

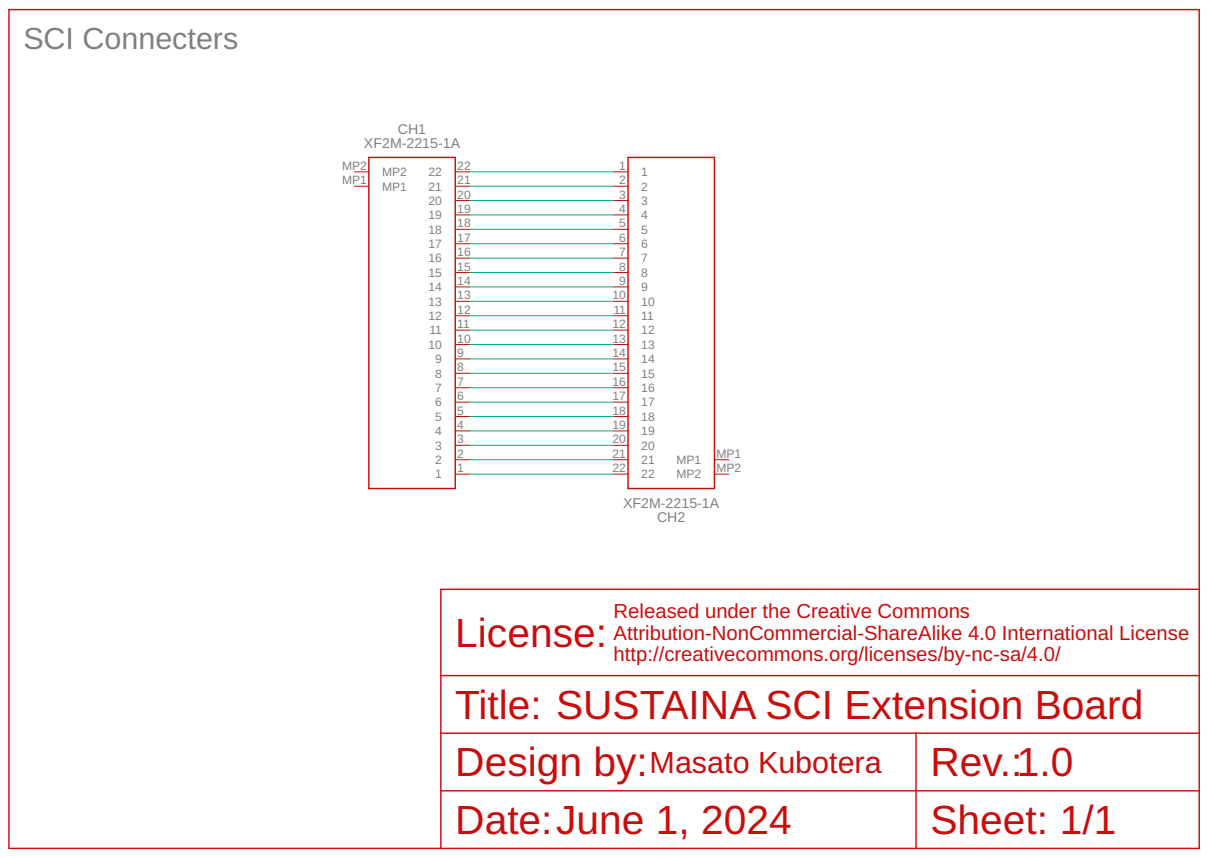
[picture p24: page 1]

Released under the Creative Commons
Attribution-NonCommercial-ShareAlike 4.0 International License
SUSTAINA SCI Extension Board

http://creativecommons.org/licenses/by-nc-sa/4.0/ License:

Design by: Masato Kubotera | Rev.: 1.0
Date: June 1, 2024 | Sheet: 1/1

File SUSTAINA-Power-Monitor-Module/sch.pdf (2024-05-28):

# I2C Address Selection by Shortland

# Current-shunt and power monitor

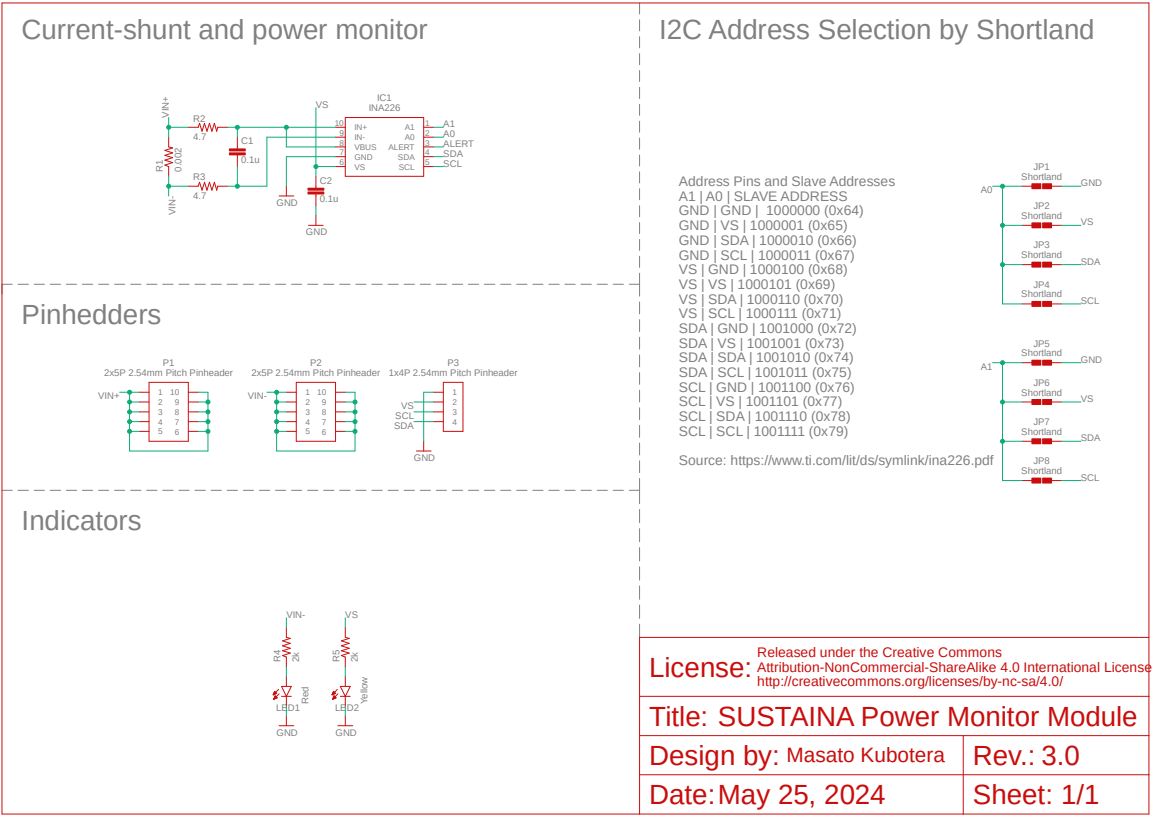
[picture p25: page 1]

Address Pins and Slave Addresses
A1 | A0 | SLAVE ADDRESS
GND | GND | 1000000 (0x64)
GND | VS | 1000001 (0x65)
GND | SDA | 1000010 (0x66)
GND | SCL | 1000011 (0x67)
VS | GND | 1000100 (0x68)
VS | SDA | 1000110 (0x70)
VS | SCL | 1000111 (0x71)
SDA | GND | 1001000 (0x72)
SDA | VS | 1001001 (0x73)
SDA | SDA | 1001010 (0x74)
SDA | SCL | 1001011 (0x75)
SCL | GND | 1001100 (0x76)
SCL | VS | 1001101 (0x77)
SCL | SDA | 1001110 (0x78)

Source: https://www.ti.com/lit/ds/symlink/ina226.pdf

http://creativecommons.org/licenses/by-nc-sa/4.0/ License:
Title:

Released under the Creative Commons
Attribution-NonCommercial-ShareAlike 4.0 International License
SUSTAINA Power Monitor Module

Design by: Masato Kubotera | Rev.: 3.0
Date: May 25, 2024 | Sheet: 1/1

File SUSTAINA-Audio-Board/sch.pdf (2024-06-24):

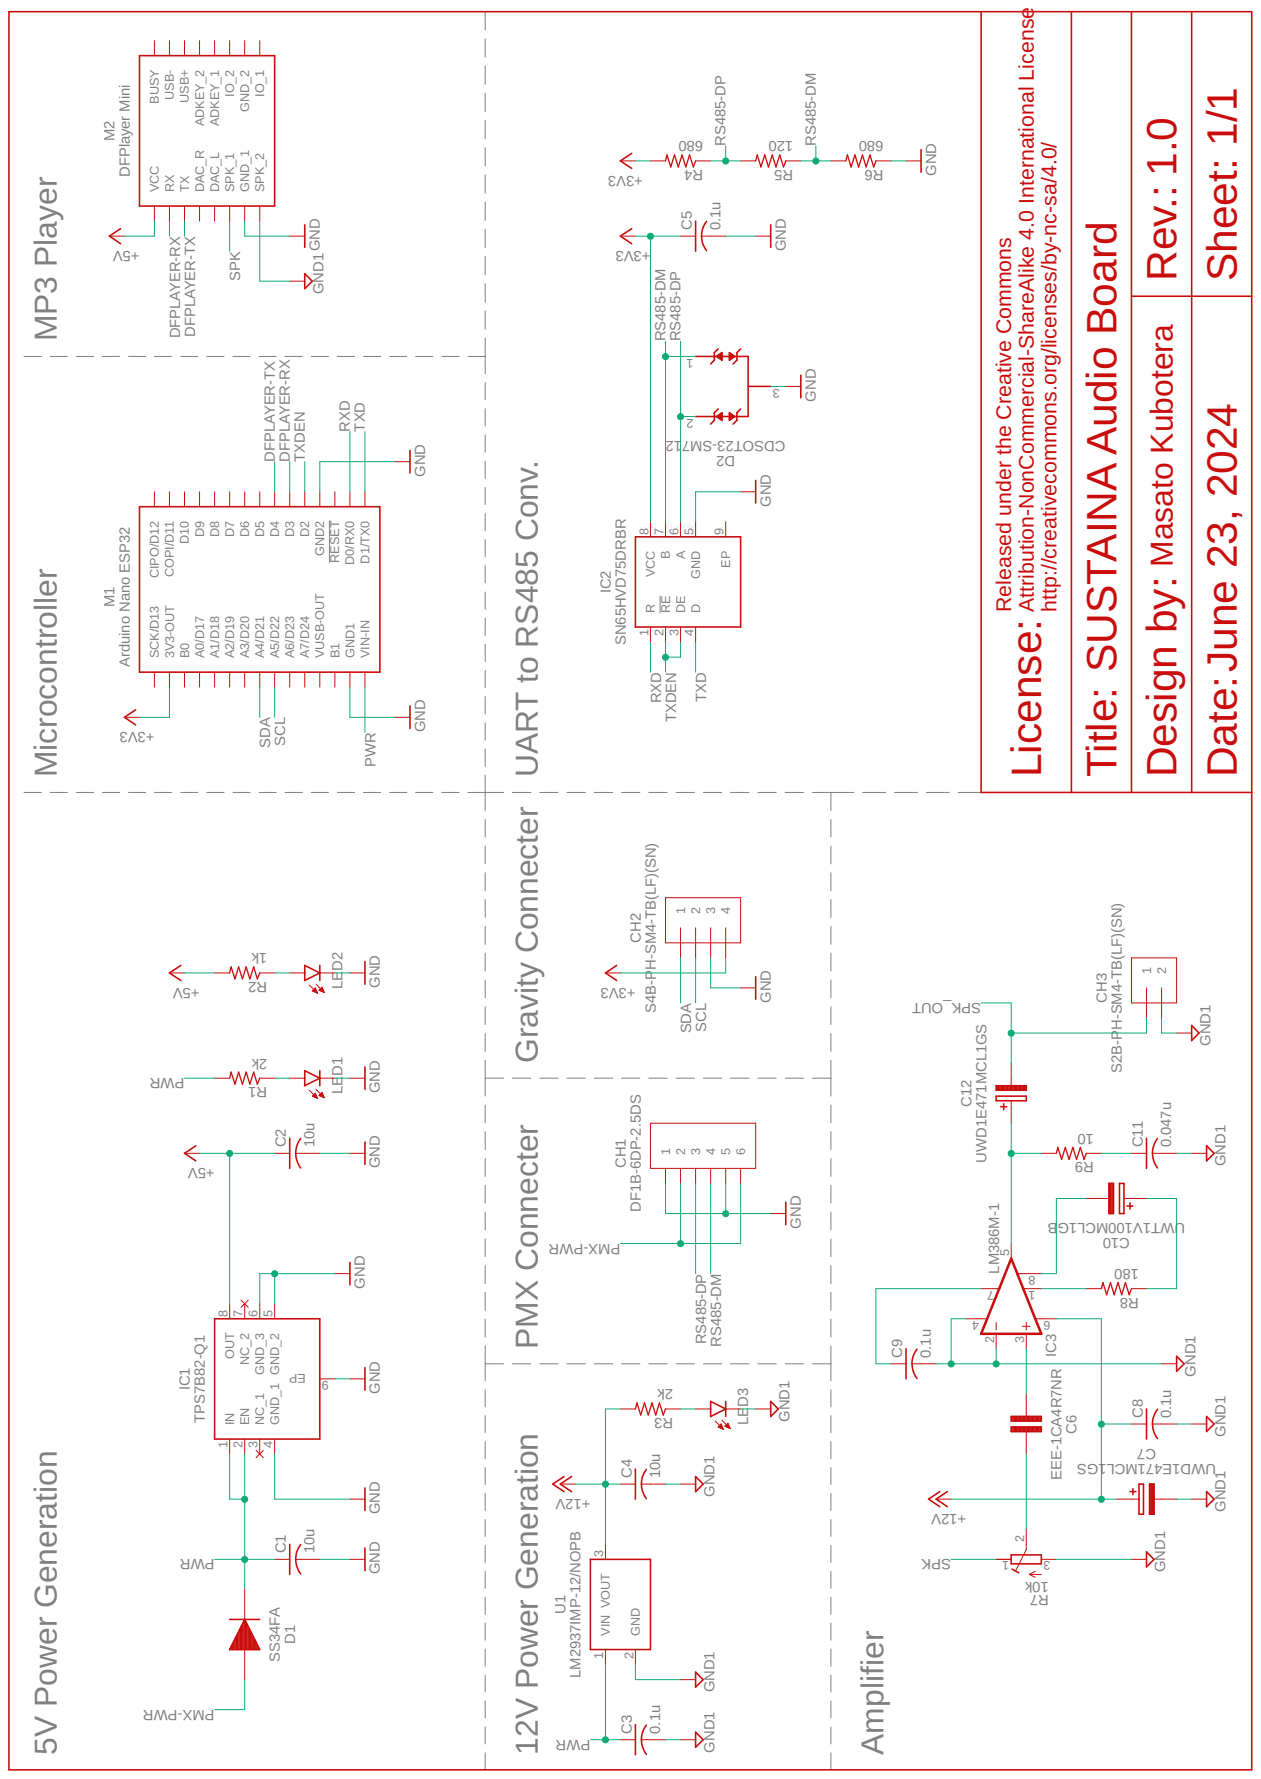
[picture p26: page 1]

ons.org/licenses/by-nc-sa/4.0/ Lic

DFPLAYER-RX DFPLAYER-TX DFPLAYER-TX

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

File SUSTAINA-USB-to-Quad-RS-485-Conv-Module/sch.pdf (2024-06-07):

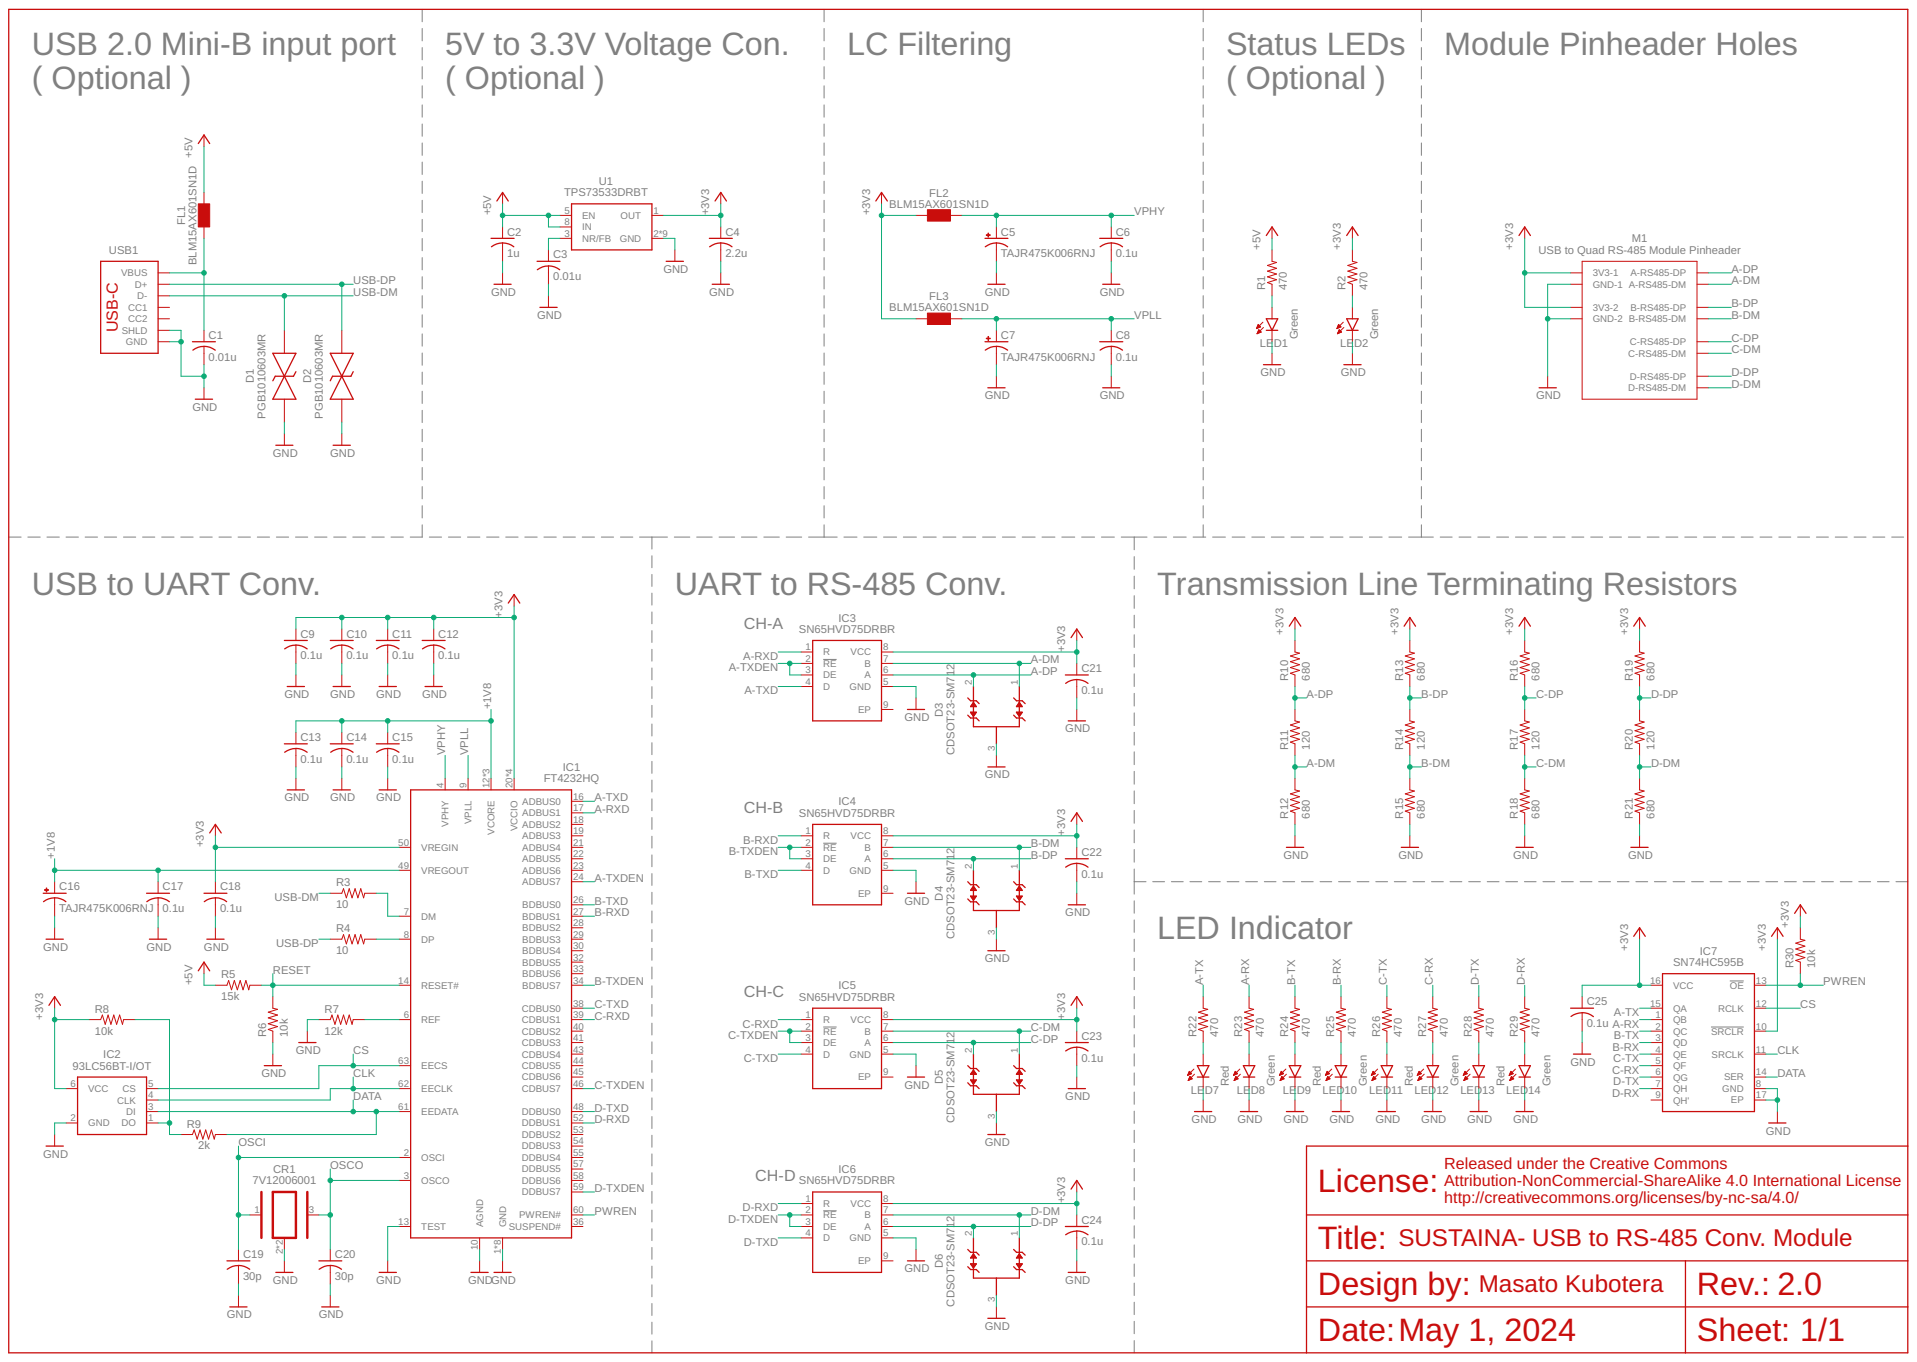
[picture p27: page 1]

USB 2.0 Mini-B input port
( Optional )

USB to Quad RS-485 Module Pinheader

Transmission Line Terminating Resistors

Released under the Creative Commons Attribution-NonCommercial-ShareAlike 4.0 International License

http://creativecommons.org/licenses/by-nc-sa/4.0/ License:

SUSTAINA- USB to RS-485 Conv. Module

Design by: Masato Kubotera | Rev.:
Date: May 1, 2024 | Sheet: 1/1

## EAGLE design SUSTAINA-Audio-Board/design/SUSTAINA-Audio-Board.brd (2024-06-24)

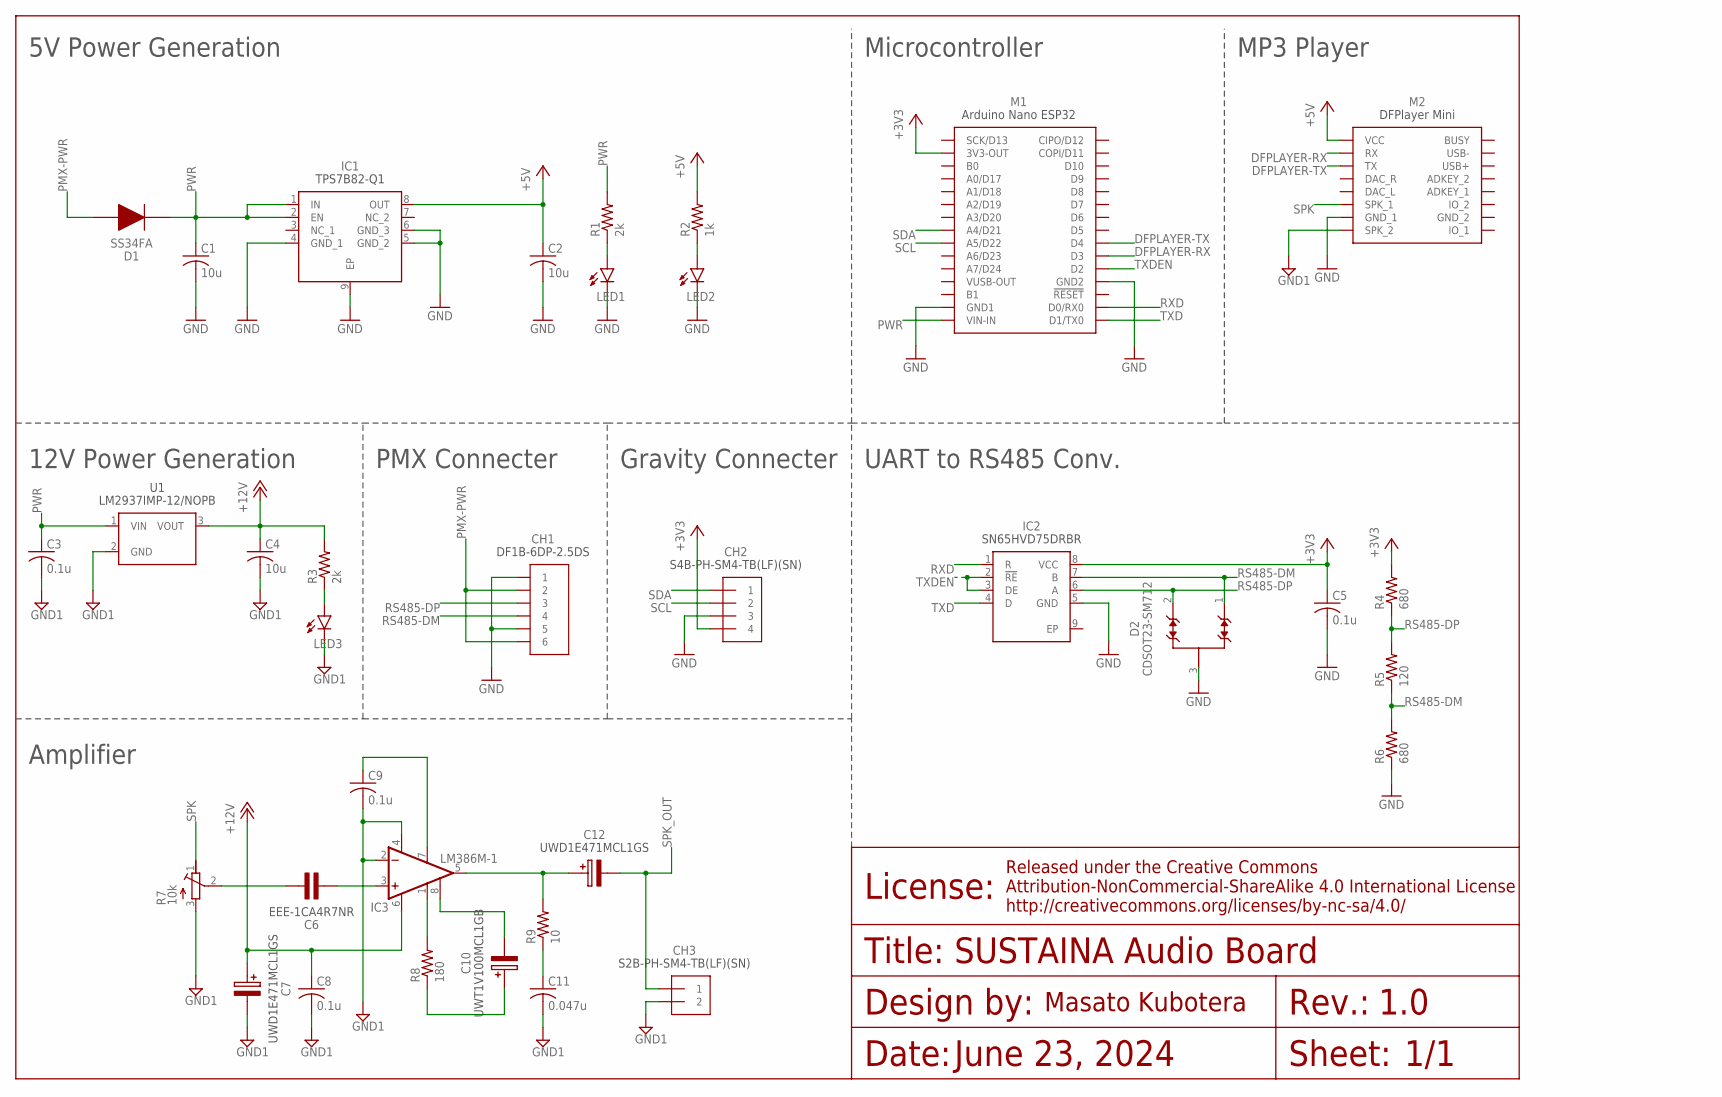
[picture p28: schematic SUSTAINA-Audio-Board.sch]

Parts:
C1, C2, C4: 10u; C0603
C3, C5, C8, C9: 0.1u; C0603
C6: EEE-1CA4R7NR
C7, C12: UWD1E471MCL1GS
C10: UWT1V100MCL1GB
C11: 0.047u; C050-055X075
CH1: DF1B-6DP-2.5DS
CH2: S4B-PH-SM4-TB(LF)(SN)
CH3: S2B-PH-SM4-TB(LF)(SN)
D1: SS34FA
D2: CDSOT23-SM712; SOT-23-3
IC1: TPS7B82-Q1; SOP65P490X110-9N
IC2: SN65HVD75DRBR; SON65P300X300X100-9N
IC3: LM386M-1; SO08
LED1, LED2, LED3: LEDSML0603; SML0603
M1: NANO-ESP32
M2: DFPLAYER_MINI
R1, R3: 2k; R0603
R2: 1k; R0603
R4, R6: 680; R0603
R5: 120; R0603
R7: 10k; RTRIM3006P
R8: 180; R0603
R9: 10; R0603
U1: LM2937IMP-12NOPB; SOT-223

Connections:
+3V3: C5.1, CH2.4, IC2.8 (VCC), M1.3V3-OUT, R4.2
+5V: C2.1, IC1.8 (OUT), M2.VCC, R2.2
+12V: C4.1, C7.+, C8.1, IC3.6 (VS), R3.2, U1.3 (VOUT)
DFPLAYER-RX: M1.D3, M2.RX
DFPLAYER-TX: M1.D4, M2.TX
GND: C1.2, C2.2, C5.2, CH1.1, CH1.5, CH2.3, D2.3, IC1.4 (GND_1), IC1.5 (GND_2), IC1.6 (GND_3), IC1.9 (EP), IC2.5 (GND), LED1.C, LED2.C, M1.GND1, M1.GND2, M2.GND_1, R6.1
GND1: C3.2, C4.2, C7.-, C8.2, C9.2, C11.2, CH3.2, IC3.2 (-IN), IC3.4 (GND), LED3.C, M2.SPK2 (SPK_2), R7.3 (A), U1.2 (GND)
LED-5V: LED2.A, R2.1
LED-12V: LED3.A, R3.1
LED-VIN: LED1.A, R1.1
LM386_1: IC3.1 (GAIN), R8.2
LM386_1-8: C10.+, R8.1
LM386_3: C6.1, IC3.3 (+IN)
LM386_3_: C6.2, R7.2 (S)
LM386_7: C9.1, IC3.7 (BYPASS)
LM386_8: C10.-, IC3.8 (GAIN)
PMX-PWR: CH1.2, CH1.6, D1.2
PWR: C1.1, C3.1, D1.1, IC1.1 (IN), IC1.2 (EN), M1.VIN-IN, R1.2, U1.1 (VIN)
RS485-DM: CH1.4, D2.1, IC2.7 (B), R5.1, R6.2
RS485-DP: CH1.3, D2.2, IC2.6 (A), R4.1, R5.2
RXD: IC2.1 (R), M1.D0/RX0
SCL: CH2.2, M1.A5/D22
SDA: CH2.1, M1.A4/D21
SPK: M2.SPK1 (SPK_1), R7.1 (E)
SPK_OUT: C12.-, CH3.1
SPK_OUT_: C12.+, IC3.5 (OUT), R9.2
SPK_OUT__: C11.1, R9.1
TXD: IC2.4 (D), M1.D1/TX0
TXDEN: IC2.2 (!RE), IC2.3 (DE), M1.D2

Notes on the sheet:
1.0
1/1
June 23, 2024
SUSTAINA Audio Board
5V Power Generation
12V Power Generation
PMX Connecter
Gravity Connecter
Amplifier
UART to RS485 Conv.
Microcontroller
MP3 Player

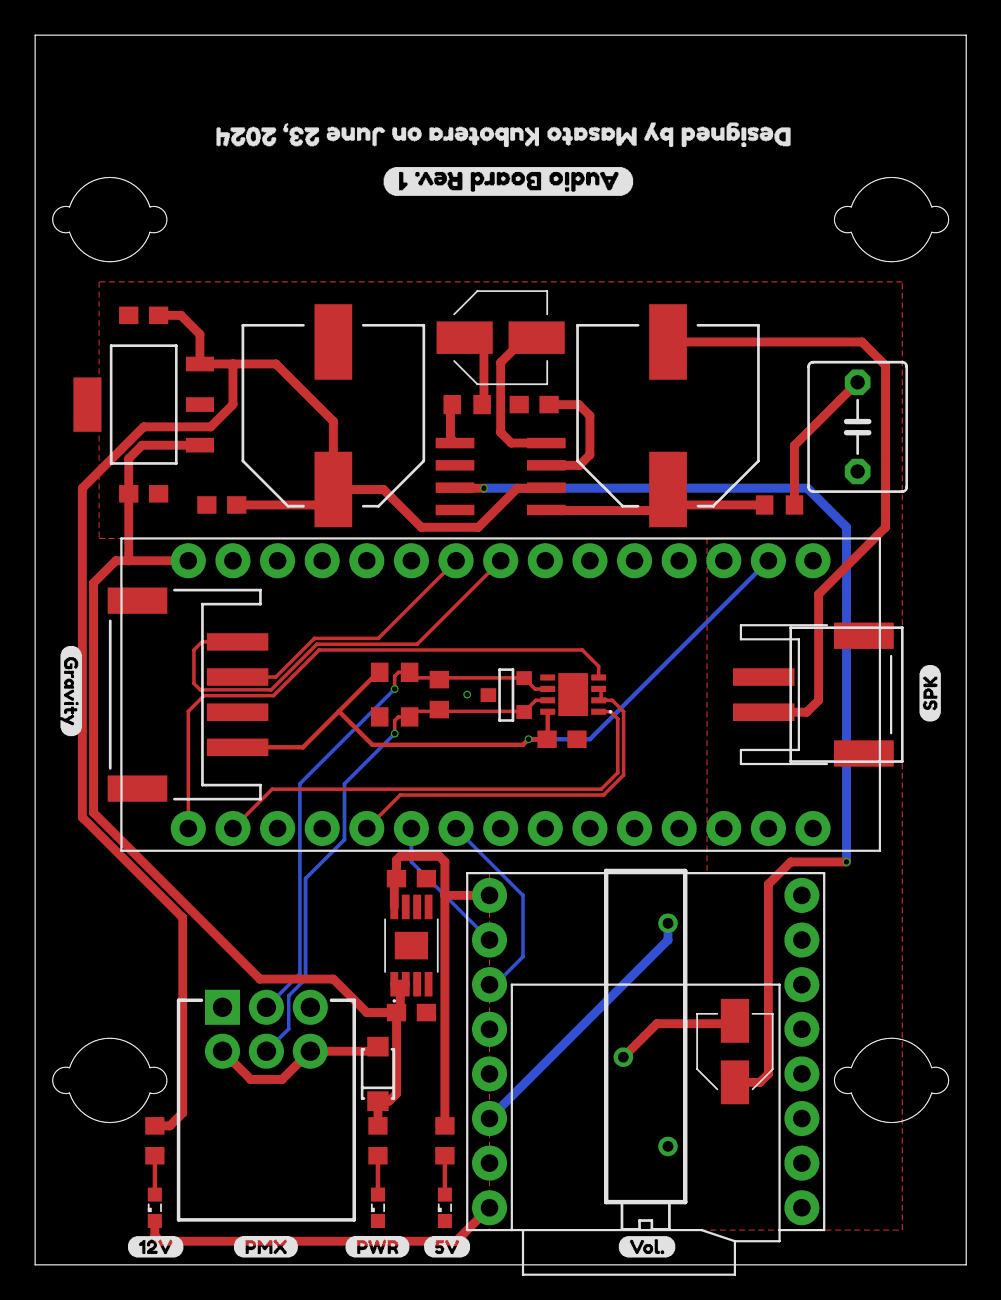
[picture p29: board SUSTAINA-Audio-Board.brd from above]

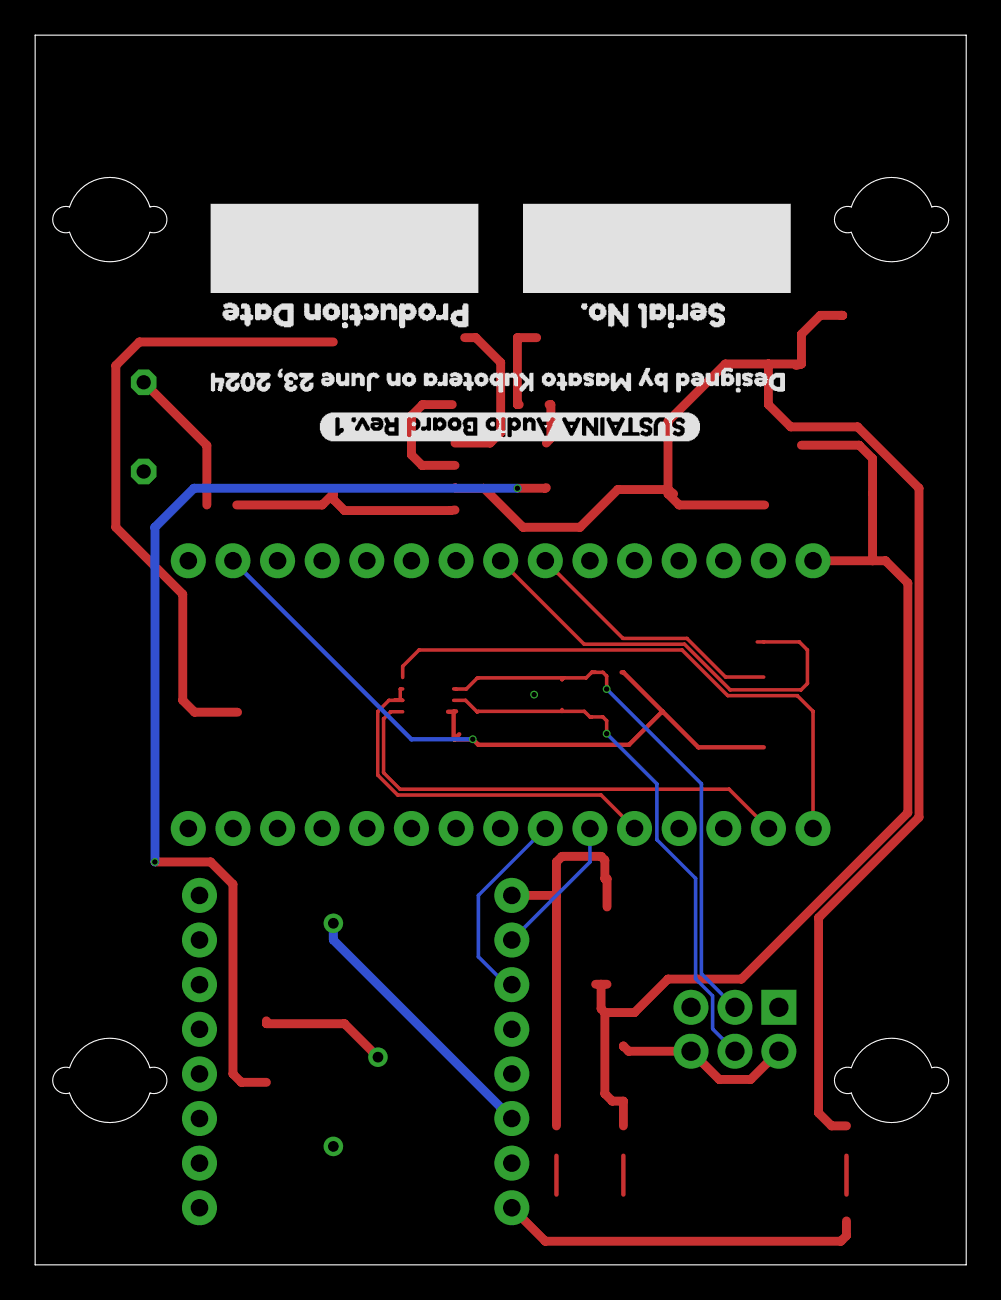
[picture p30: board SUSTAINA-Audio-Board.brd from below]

Board: 2 copper layers, 53.0 x 70.0 mm, 48 parts (4 on the bottom side), 29 nets.

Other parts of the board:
U$1: GRAVITY-0.03
U$2, U$11: DESIGNED_BY_MASATO_KUBOTERA_ON_JUNE_23
U$3: 12V-0.03
U$4: 5V-0.03
U$5: PMX-0.03
U$6: PWR-0.03
U$7: VOL#-0.03
U$8: SPK-0.03
U$9: SUSTAINA_AUDIO_BOARD_REV#_1
U$10: AUDIO_BOARD_REV#_1
U$12: PRODUCTION_DATE0
U$13: SERIAL_NO#0

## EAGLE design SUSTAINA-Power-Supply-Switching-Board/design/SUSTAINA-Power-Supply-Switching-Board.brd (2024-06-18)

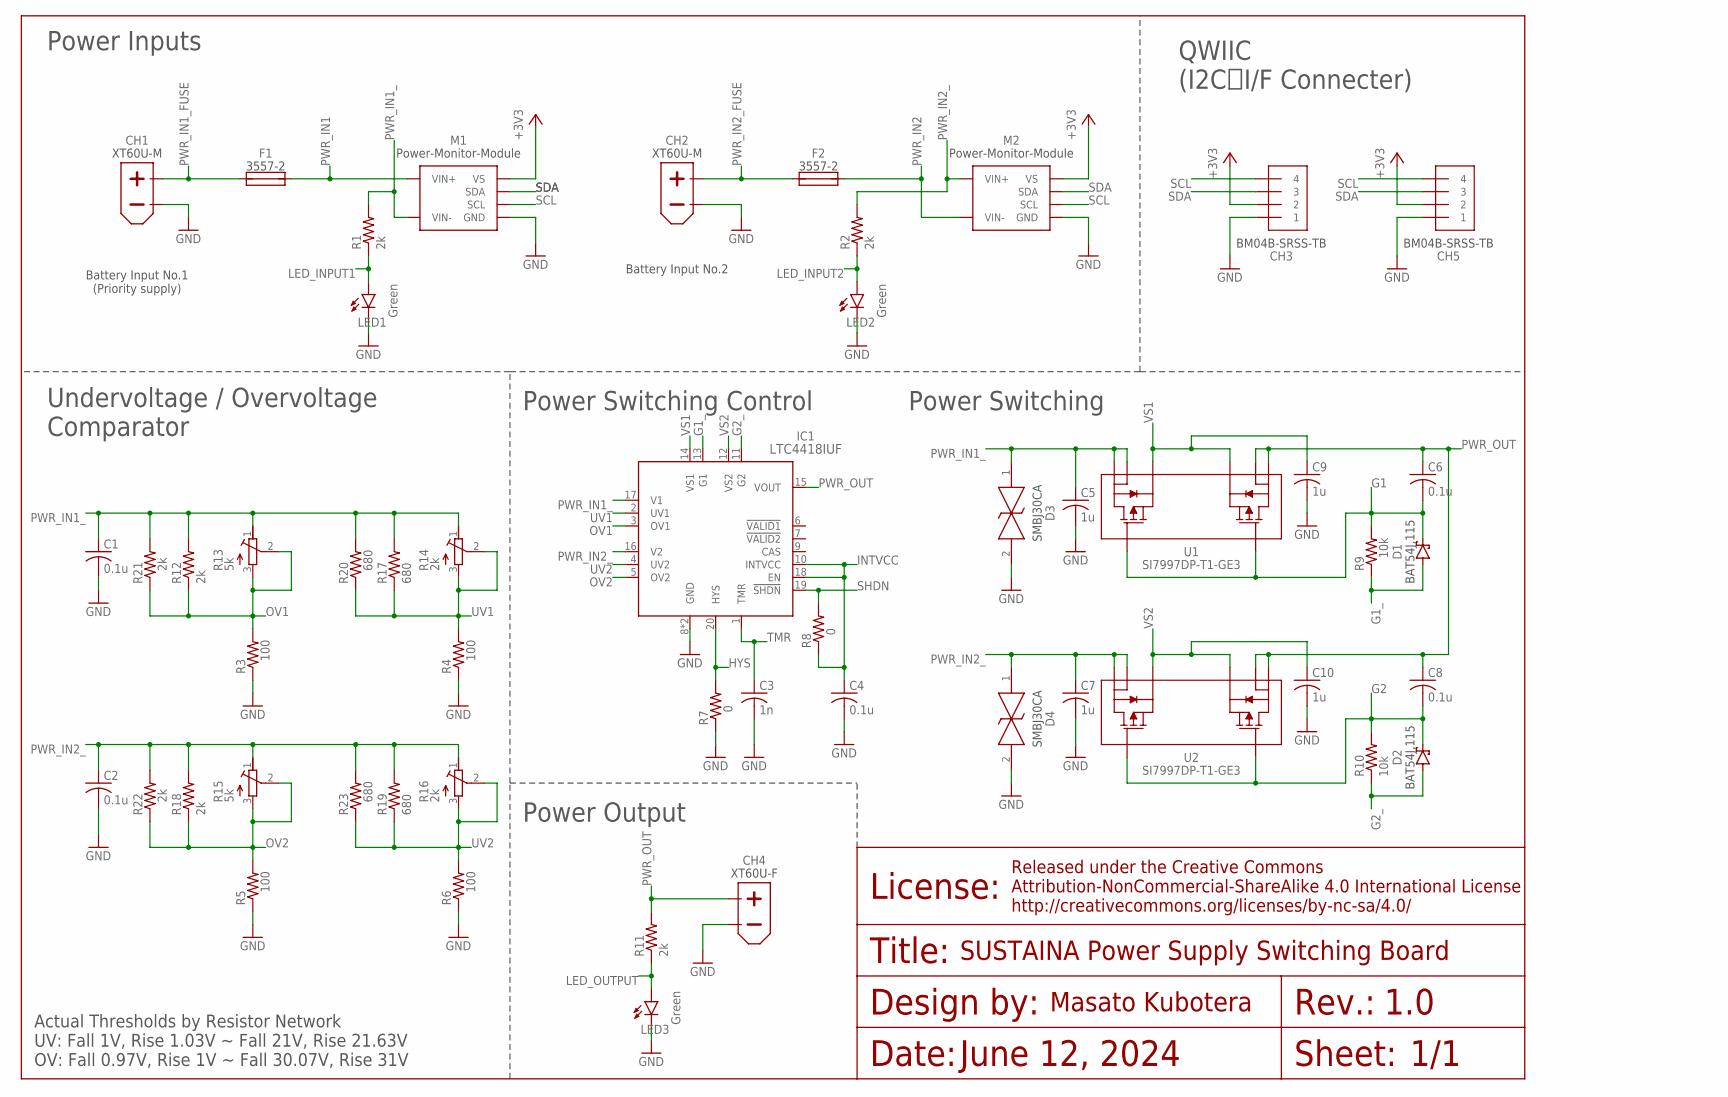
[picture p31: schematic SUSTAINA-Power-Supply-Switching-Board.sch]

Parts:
C1, C2, C4, C6, C8: 0.1u; C0603
C3: 1n; C0603
C5, C7, C9, C10: 1u; C0603
CH1, CH2: XT60U-M
CH3, CH5: BM04B-SRSS-TB
CH4: XT60U-F
D1, D2: BAT54J,115; SOD-323-2
D3, D4: SMBJ30CA
F1, F2: 3557-2
IC1: LTC4418IUF
LED1, LED2, LED3: Green; SML0603
M1, M2: POWER-MONITOR-MODULE
R1, R2, R11, R21, R22: 2k; R0603
R3, R4, R5, R6: 100; R0603
R7, R8: 0; R0603
R9, R10: 10k; R0603
R12, R18: 2k; 0204/5
R13, R15: 5k; RTRIM3006P
R14, R16: 2k; RTRIM3006P
R17, R19: 680; 0204/5
R20, R23: 680; R0603
U1, U2: SI7997DP-T1-GE3; POWERPAK_SO-8_VIS

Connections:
+3V3: CH3.2, CH5.2, M1.VS, M2.VS
G1: C6.2, D1.1 (C), R9.2, U1.2 (G1), U1.4 (G2)
G1_: D1.2 (A), IC1.13 (G1), R9.1
G2: C8.2, D2.1 (C), R10.2, U2.2 (G1), U2.4 (G2)
G2_: D2.2 (A), IC1.11 (G2), R10.1
GND: C1.2, C2.2, C3.2, C4.2, C5.2, C7.2, C9.2, C10.2, CH1.-, CH2.-, CH3.1, CH4.-, CH5.1, D3.2, D4.2, IC1.8 (GND), IC1.21 (GND), LED1.C, LED2.C, LED3.C, M1.GND, M2.GND, R3.1, R4.1, R5.1, R6.1, R7.1
HYS: IC1.20 (HYS), R7.2
INTVCC: C4.1, IC1.10 (INTVCC), IC1.18 (EN), R8.1
LED_INPUT1: LED1.A, R1.1
LED_INPUT2: LED2.A, R2.1
LED_OUTPUT: LED3.A, R11.1
OV1: IC1.3 (OV1), R3.2, R12.1, R13.2 (S), R13.3 (A), R21.1
OV2: IC1.5 (OV2), R5.2, R15.2 (S), R15.3 (A), R18.1, R22.1
PWR_IN1: F1.3 (2), F1.4 (2), M1.VIN+1 (VIN+), M1.VIN+2 (VIN+), M1.VIN+3 (VIN+), M1.VIN+4 (VIN+), M1.VIN+5 (VIN+), M1.VIN+6 (VIN+), M1.VIN+7 (VIN+), M1.VIN+8 (VIN+), M1.VIN+9 (VIN+), M1.VIN+10 (VIN+)
PWR_IN1_: C1.1, C5.1, D3.1, IC1.17 (V1), M1.VIN-1 (VIN-), M1.VIN-2 (VIN-), M1.VIN-3 (VIN-), M1.VIN-4 (VIN-), M1.VIN-5 (VIN-), M1.VIN-6 (VIN-), M1.VIN-7 (VIN-), M1.VIN-8 (VIN-), M1.VIN-9 (VIN-), M1.VIN-10 (VIN-), R1.2, R12.2, R13.1 (E), R14.1 (E), R17.2, R20.2, R21.2, U1.5 (D2), U1.6 (D2_2)
PWR_IN1_FUSE: CH1.+, F1.1, F1.2 (1)
PWR_IN2: F2.3 (2), F2.4 (2), M2.VIN-1 (VIN-), M2.VIN-2 (VIN-), M2.VIN-3 (VIN-), M2.VIN-4 (VIN-), M2.VIN-5 (VIN-), M2.VIN-6 (VIN-), M2.VIN-7 (VIN-), M2.VIN-8 (VIN-), M2.VIN-9 (VIN-), M2.VIN-10 (VIN-)
PWR_IN2_: C2.1, C7.1, D4.1, IC1.16 (V2), M2.VIN+1 (VIN+), M2.VIN+2 (VIN+), M2.VIN+3 (VIN+), M2.VIN+4 (VIN+), M2.VIN+5 (VIN+), M2.VIN+6 (VIN+), M2.VIN+7 (VIN+), M2.VIN+8 (VIN+), M2.VIN+9 (VIN+), M2.VIN+10 (VIN+), R2.2, R15.1 (E), R16.1 (E), R18.2, R19.2, R22.2, R23.2, U2.7 (D1), U2.8 (D1_2)
PWR_IN2_FUSE: CH2.+, F2.1, F2.2 (1)
PWR_OUT: C6.1, C8.1, CH4.+, IC1.15 (VOUT), R11.2, U1.7 (D1), U1.8 (D1_2), U2.5 (D2), U2.6 (D2_2)
SCL: CH3.4, CH5.4, M1.SCL, M2.SCL
SDA: CH3.3, CH5.3, M1.SDA, M2.SDA
SHDN: IC1.19 (!SHDN), R8.2
TMR: C3.1, IC1.1 (TMR)
UV1: IC1.2 (UV1), R4.2, R14.2 (S), R14.3 (A), R17.1, R20.1
UV2: IC1.4 (UV2), R6.2, R16.2 (S), R16.3 (A), R19.1, R23.1
VS1: C9.1, IC1.14 (VS1), U1.1 (S1), U1.3 (S2)
VS2: C10.1, IC1.12 (VS2), U2.1 (S1), U2.3 (S2)

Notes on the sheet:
Battery Input No.1 (Priority supply)
Battery Input No.2
Actual Thresholds by Resistor Network UV: Fall 1V, Rise 1.03V ~ Fall 21V, Rise 21.63V OV: Fall 0.97V, Rise 1V ~ Fall 30.07V, Rise 31V
1.0
1/1
June 12, 2024
SUSTAINA Power Supply Switching Board
Power Inputs
Undervoltage / Overvoltage Comparator
Power Switching Control
Power Switching
QWIIC (I2C I/F Connecter)
Power Output

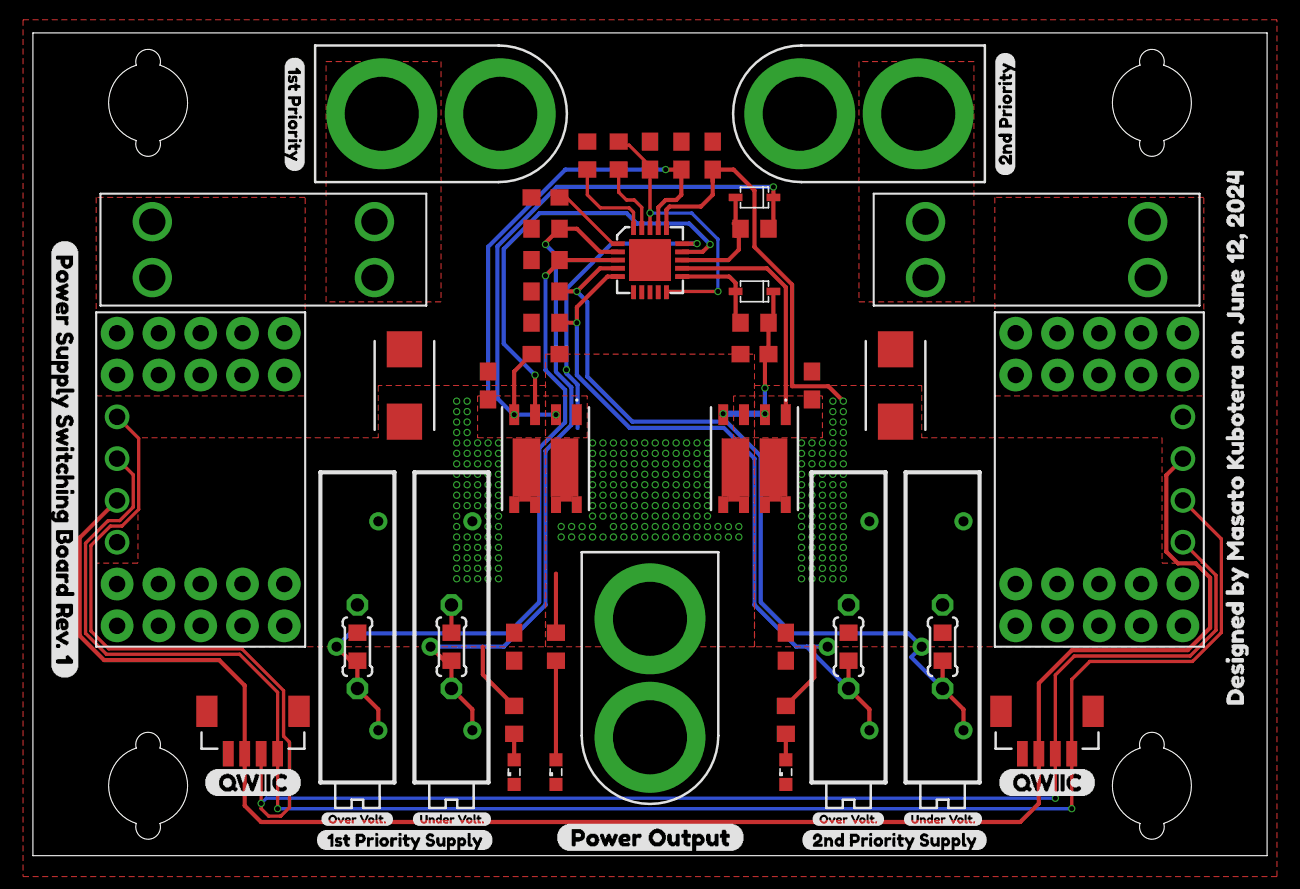
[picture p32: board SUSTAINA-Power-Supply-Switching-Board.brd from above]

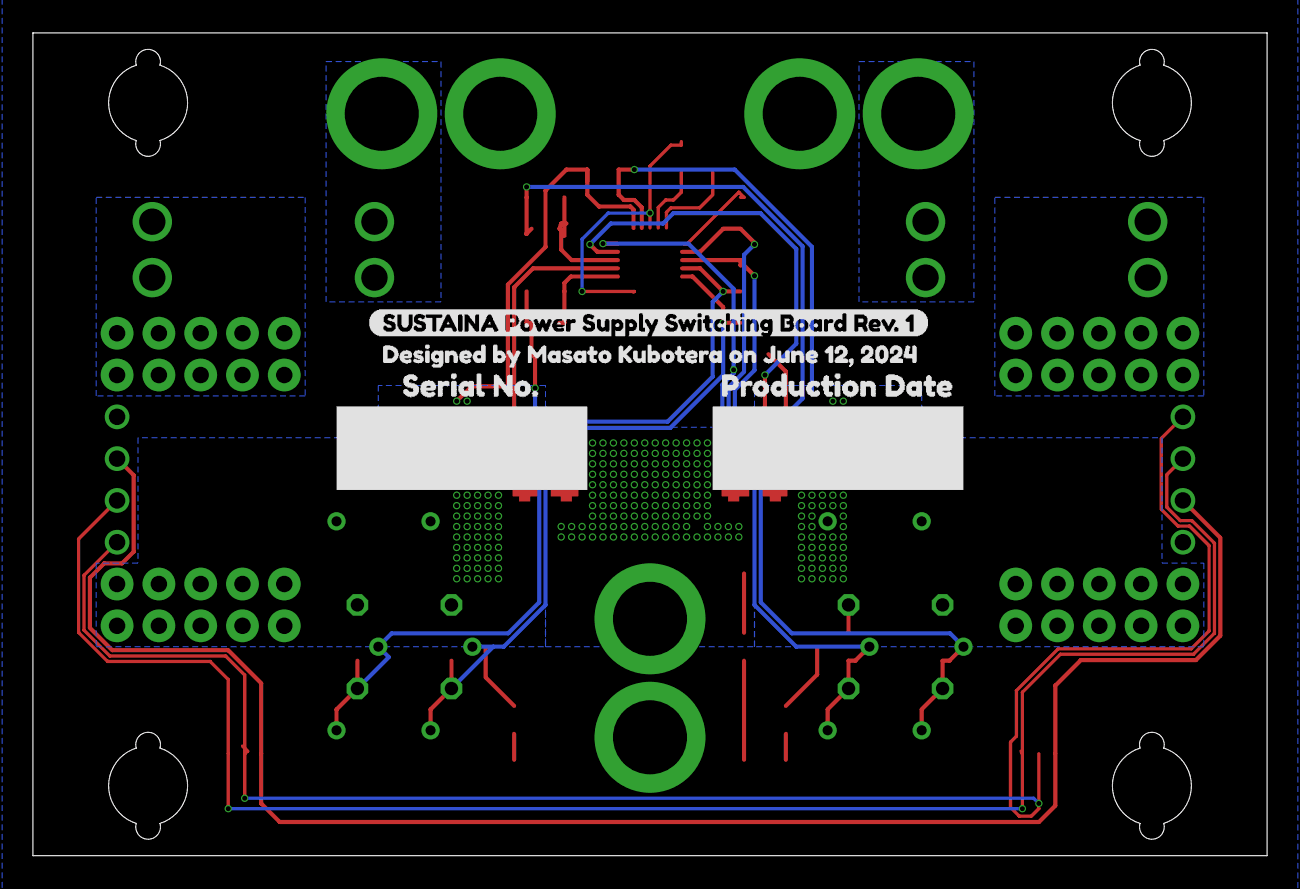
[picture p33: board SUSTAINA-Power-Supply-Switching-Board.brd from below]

Board: 2 copper layers, 75.0 x 50.0 mm, 69 parts (4 on the bottom side), 28 nets.

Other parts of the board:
U$1: SUSTAINA_POWER_SUPPLY_SWITCHING_BOARD_REV#_1
U$2, U$15: DESIGNED_BY_MASATO_KUBOTERA_ON_JUNE_12
U$3: 1ST_PRIORITY
U$4: 2ND_PRIORITY
U$5: POWER_OUTPUT0
U$6: 1ST_PRIORITY_SUPPLY1
U$7: 2ND_PRIORITY_SUPPLY1
U$8, U$9: UNDER_VOLT#0
U$10, U$11: OVER_VOLT#0
U$12, U$13: QWIIC0
U$14: POWER_SUPPLY_SWITCHING_BOARD_REV#_1
U$16: SERIAL_NO#0
U$29: PRODUCTION_DATE0

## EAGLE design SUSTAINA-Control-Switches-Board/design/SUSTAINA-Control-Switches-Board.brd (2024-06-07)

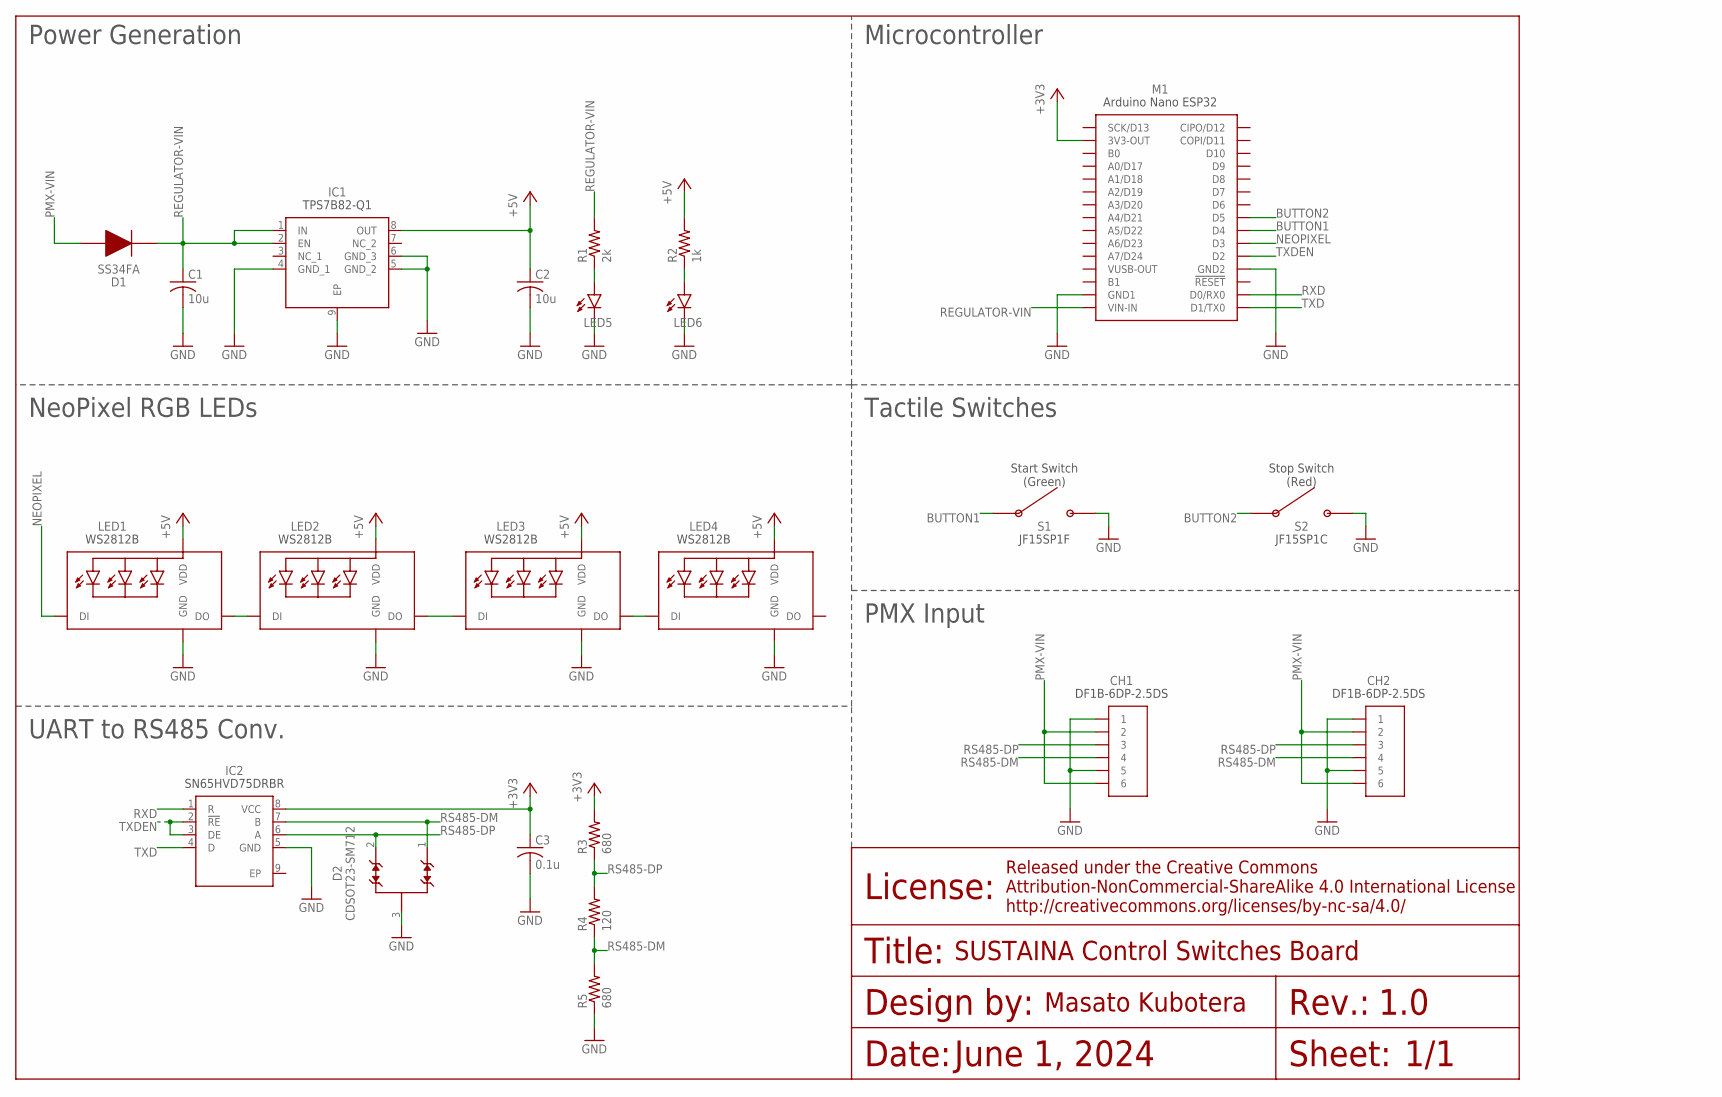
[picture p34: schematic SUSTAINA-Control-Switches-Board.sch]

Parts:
C1, C2: 10u; C0603
C3: 0.1u; C0603
CH1, CH2: DF1B-6DP-2.5DS
D1: SS34FA
D2: CDSOT23-SM712; SOT-23-3
IC1: TPS7B82-Q1; SOP65P490X110-9N
IC2: SN65HVD75DRBR; SON65P300X300X100-9N
LED1, LED2, LED3, LED4: WS2812B
LED5, LED6: LEDSML0603; SML0603
M1: NANO-ESP32
R1: 2k; R0603
R2: 1k; R0603
R3, R5: 680; R0603
R4: 120; R0603
S1: JF15SP1F; JF15SP1
S2: JF15SP1C; JF15SP1

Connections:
+3V3: C3.1, IC2.8 (VCC), M1.3V3-OUT, R3.2
+5V: C2.1, IC1.8 (OUT), LED1.1-VDD (VDD), LED2.1-VDD (VDD), LED3.1-VDD (VDD), LED4.1-VDD (VDD), R2.2
BUTTON1: M1.D4, S1.1, S1.2
BUTTON2: M1.D5, S2.1, S2.2
DO-DI-1: LED1.2-DOUT (DO), LED2.4-DIN (DI)
DO-DI-2: LED2.2-DOUT (DO), LED3.4-DIN (DI)
DO-DI-3: LED3.2-DOUT (DO), LED4.4-DIN (DI)
GND: C1.2, C2.2, C3.2, CH1.1, CH1.5, CH2.1, CH2.5, D2.3, IC1.4 (GND_1), IC1.5 (GND_2), IC1.6 (GND_3), IC1.9 (EP), IC2.5 (GND), LED1.3-GND (GND), LED2.3-GND (GND), LED3.3-GND (GND), LED4.3-GND (GND), LED5.C, LED6.C, M1.GND1, M1.GND2, R5.1, S1.3, S1.4, S2.3, S2.4
LED-D-RX: LED6.A, R2.1
LED-D-TX: LED5.A, R1.1
NEOPIXEL: LED1.4-DIN (DI), M1.D3
PMX-VIN: CH1.2, CH1.6, CH2.2, CH2.6, D1.2
REGULATOR-VIN: C1.1, D1.1, IC1.1 (IN), IC1.2 (EN), M1.VIN-IN, R1.2
RS485-DM: CH1.4, CH2.4, D2.1, IC2.7 (B), R4.1, R5.2
RS485-DP: CH1.3, CH2.3, D2.2, IC2.6 (A), R3.1, R4.2
RXD: IC2.1 (R), M1.D0/RX0
TXD: IC2.4 (D), M1.D1/TX0
TXDEN: IC2.2 (!RE), IC2.3 (DE), M1.D2

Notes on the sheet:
Start Switch (Green)
Stop Switch (Red)
Tactile Switches
1.0
1/1
June 1, 2024
SUSTAINA Control Switches Board
Power Generation
Microcontroller
NeoPixel RGB LEDs
PMX Input
UART to RS485 Conv.

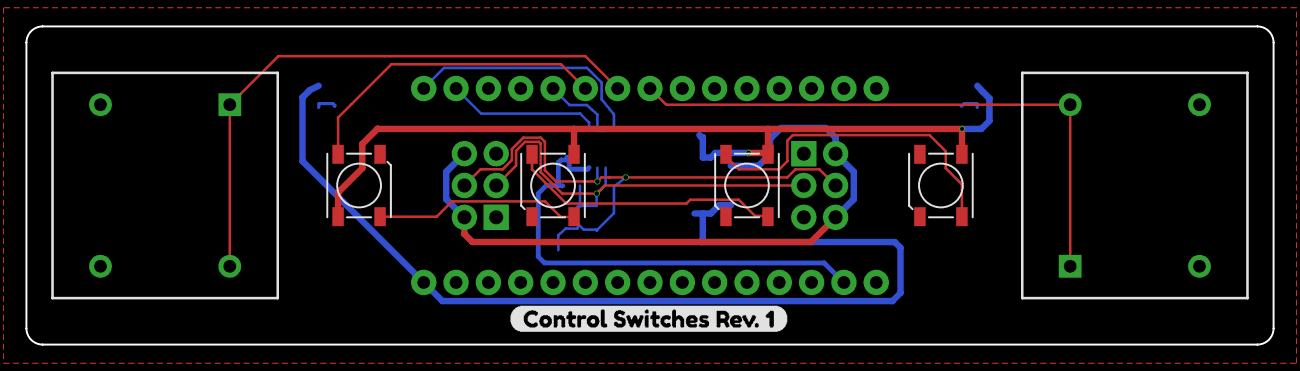
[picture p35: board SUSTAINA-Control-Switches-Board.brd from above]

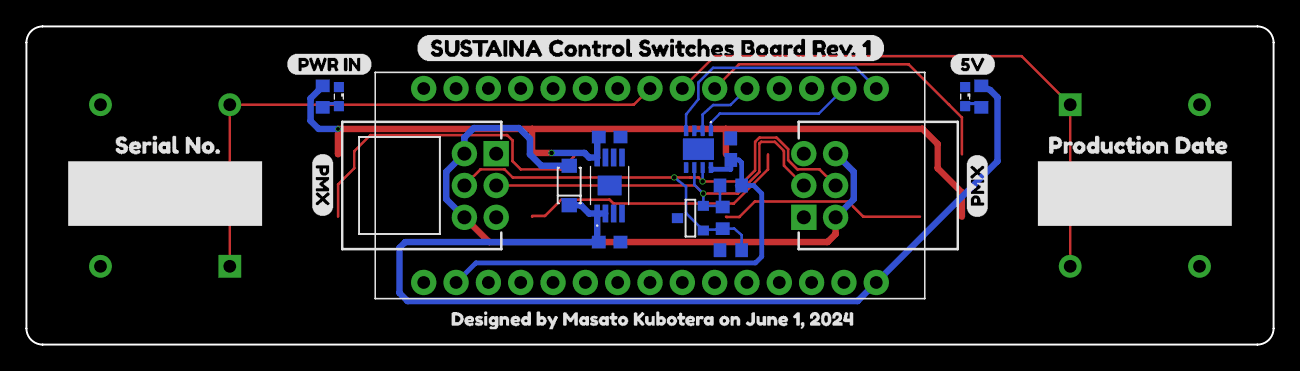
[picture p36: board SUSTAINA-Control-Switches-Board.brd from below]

Board: 2 copper layers, 98.0 x 25.0 mm, 32 parts (25 on the bottom side), 18 nets.

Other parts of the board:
U$1: SUSTAINA_CONTROL_SWITCHES_BOARD_REV#_10
U$2, U$5: PMX0
U$3: PRODUCTION_DATE0
U$4: SERIAL_NO#0
U$6: CONTROL_SWITCHES_REV#_10
U$7: PWR_IN0
U$8: 5V
U$28: DESIGNED_BY_MASATO_KUBOTERA_ON_FEBRUARY_190DESIGN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; DESIGNED_BY_MASATO_KUBOTERA_ON_JUNE_1

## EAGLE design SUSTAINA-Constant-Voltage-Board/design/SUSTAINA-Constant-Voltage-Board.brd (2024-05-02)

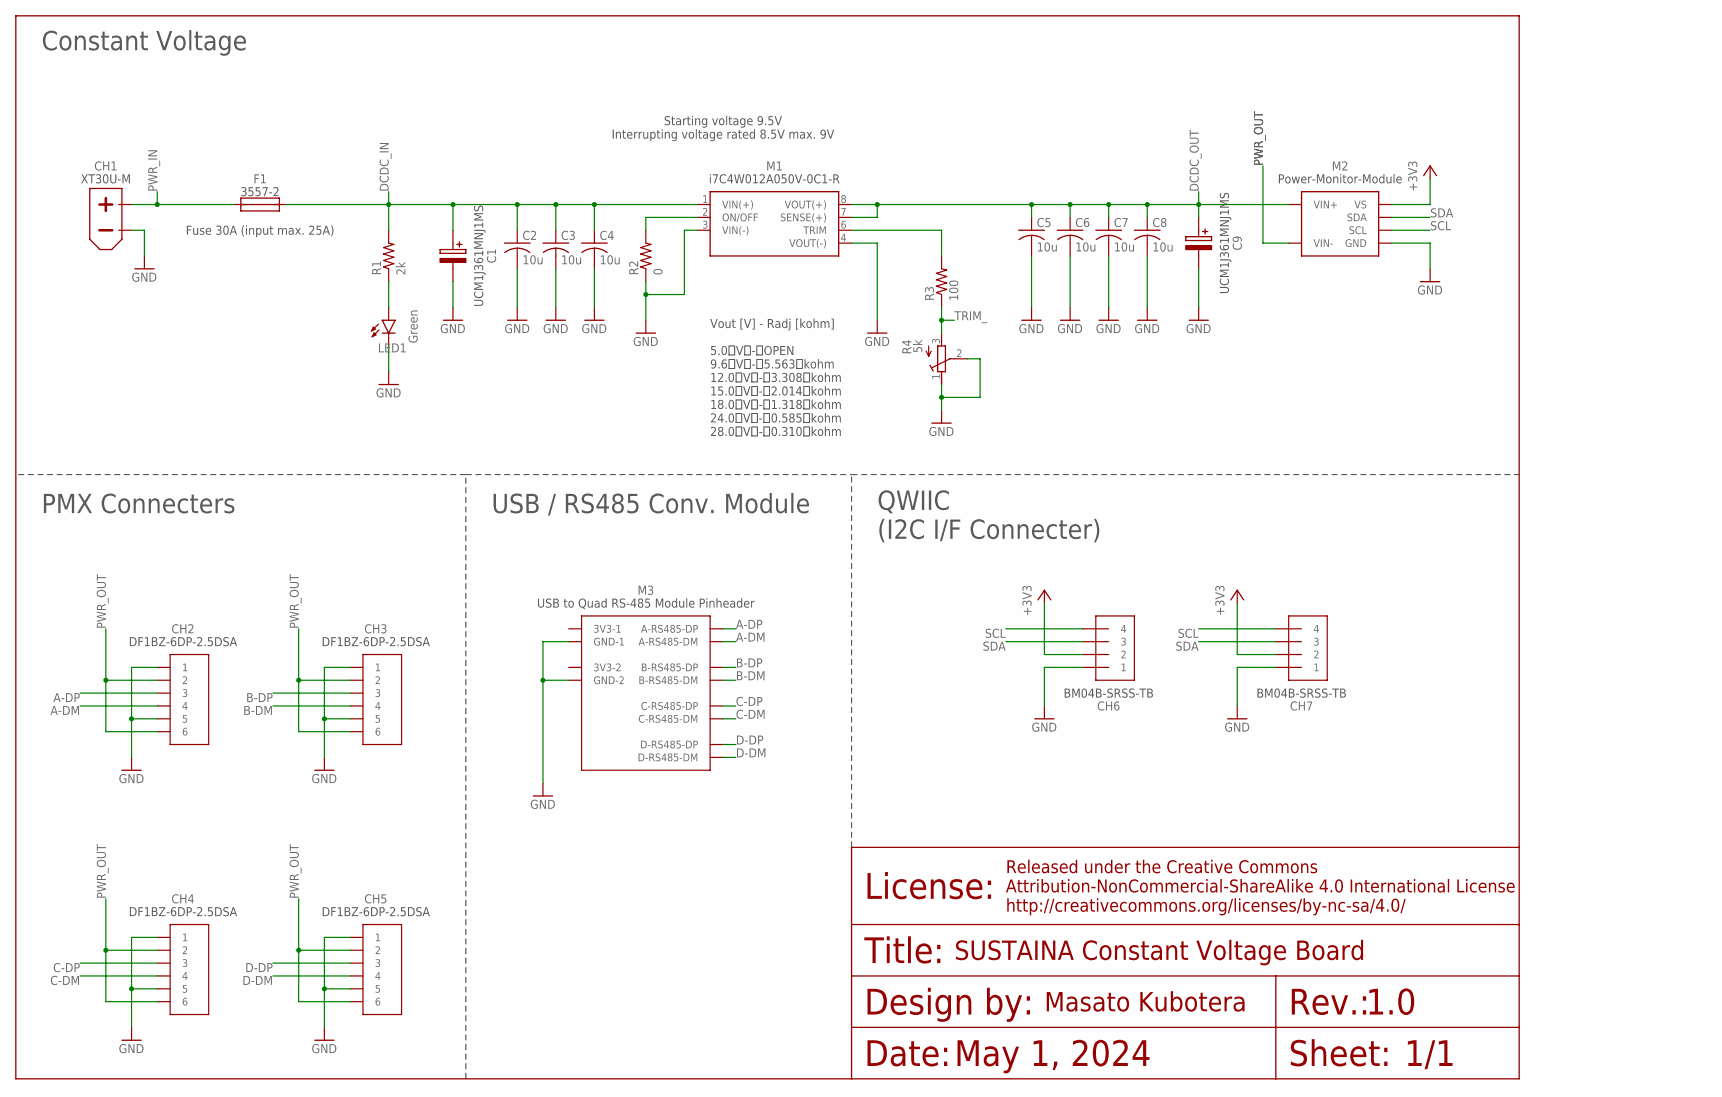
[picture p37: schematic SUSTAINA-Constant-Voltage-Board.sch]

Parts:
C1, C9: UCM1J361MNJ1MS
C2, C3, C4, C5, C6, C7, C8: 10u; C1210
CH1: XT30U-M
CH2, CH3, CH4, CH5: DF1BZ-6DP-25DSA
CH6, CH7: BM04B-SRSS-TB
F1: 3557-2
LED1: Green; SML0603
M1: I7C4W012A050V-0C1-R; I7C4W012A050V-001-R
M2: POWER-MONITOR-MODULE
M3: USB-TO-QUAD-RS-485-CONV-MODULETPLACE; USB-TO-QUAD-RS-485-CONV-MODULE-TPLACE
R1: 2k; R0603
R2: 0; R0603
R3: 100; R0603
R4: 5k; RTRIM3006P

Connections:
+3V3: CH6.2, CH7.2, M2.VS
A-DM: CH2.4, M3.A-RS-485-DM1 (A-RS485-DM), M3.A-RS-485-DM2 (A-RS485-DM)
A-DP: CH2.3, M3.A-RS-485-DP1 (A-RS485-DP), M3.A-RS-485-DP2 (A-RS485-DP)
B-DM: CH3.4, M3.B-RS-485-DM1 (B-RS485-DM), M3.B-RS-485-DM2 (B-RS485-DM)
B-DP: CH3.3, M3.B-RS-485-DP1 (B-RS485-DP), M3.B-RS-485-DP2 (B-RS485-DP)
C-DM: CH4.4, M3.C-RS-485-DM1 (C-RS485-DM), M3.C-RS-485-DM2 (C-RS485-DM)
C-DP: CH4.3, M3.C-RS-485-DP1 (C-RS485-DP), M3.C-RS-485-DP2 (C-RS485-DP)
D-DM: CH5.4, M3.D-RS-485-DM1 (D-RS485-DM), M3.D-RS-485-DM2 (D-RS485-DM)
D-DP: CH5.3, M3.D-RS-485-DP1 (D-RS485-DP), M3.D-RS-485-DP2 (D-RS485-DP)
DCDC_IN: C1.+, C2.1, C3.1, C4.1, F1.3 (2), F1.4 (2), M1.1 (VIN(+)), R1.2
DCDC_OUT: C5.1, C6.1, C7.1, C8.1, C9.+, M1.7 (SENSE(+)), M1.8 (VOUT(+)), M2.VIN+1 (VIN+), M2.VIN+2 (VIN+), M2.VIN+3 (VIN+), M2.VIN+4 (VIN+), M2.VIN+5 (VIN+), M2.VIN+6 (VIN+), M2.VIN+7 (VIN+), M2.VIN+8 (VIN+), M2.VIN+9 (VIN+), M2.VIN+10 (VIN+)
GND: C1.-, C2.2, C3.2, C4.2, C5.2, C6.2, C7.2, C8.2, C9.-, CH1.-, CH2.1, CH2.5, CH3.1, CH3.5, CH4.1, CH4.5, CH5.1, CH5.5, CH6.1, CH7.1, LED1.C, M1.3 (VIN(-)), M1.4 (VOUT(-)), M2.GND, M3.GND-1, M3.GND-2, M3.GND-3 (GND-1), M3.GND-4 (GND-2), R2.1, R4.1 (E), R4.2 (S)
LED_DCDC-IN: LED1.A, R1.1
ONOFF: M1.2 (ON/OFF), R2.2
PWR_IN: CH1.+, F1.1, F1.2 (1)
PWR_OUT: CH2.2, CH2.6, CH3.2, CH3.6, CH4.2, CH4.6, CH5.2, CH5.6, M2.VIN-1 (VIN-), M2.VIN-2 (VIN-), M2.VIN-3 (VIN-), M2.VIN-4 (VIN-), M2.VIN-5 (VIN-), M2.VIN-6 (VIN-), M2.VIN-7 (VIN-), M2.VIN-8 (VIN-), M2.VIN-9 (VIN-), M2.VIN-10 (VIN-)
SCL: CH6.4, CH7.4, M2.SCL
SDA: CH6.3, CH7.3, M2.SDA
TRIM: M1.6 (TRIM), R3.2
TRIM_: R3.1, R4.3 (A)

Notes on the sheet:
Fuse 30A (input max. 25A)
Starting voltage 9.5V Interrupting voltage rated 8.5V max. 9V
May 1, 2024
SUSTAINA Constant Voltage Board
1.0
1/1
QWIIC (I2C I/F Connecter)
USB / RS485 Conv. Module
PMX Connecters
Constant Voltage
Vout [V] - Radj [kohm] 5.0 V - OPEN 9.6 V - 5.563 kohm 12.0 V - 3.308 kohm 15.0 V - 2.014 kohm 18.0 V - 1.318 kohm 24.0 V - 0.585 kohm 28.0 V - 0.310 kohm

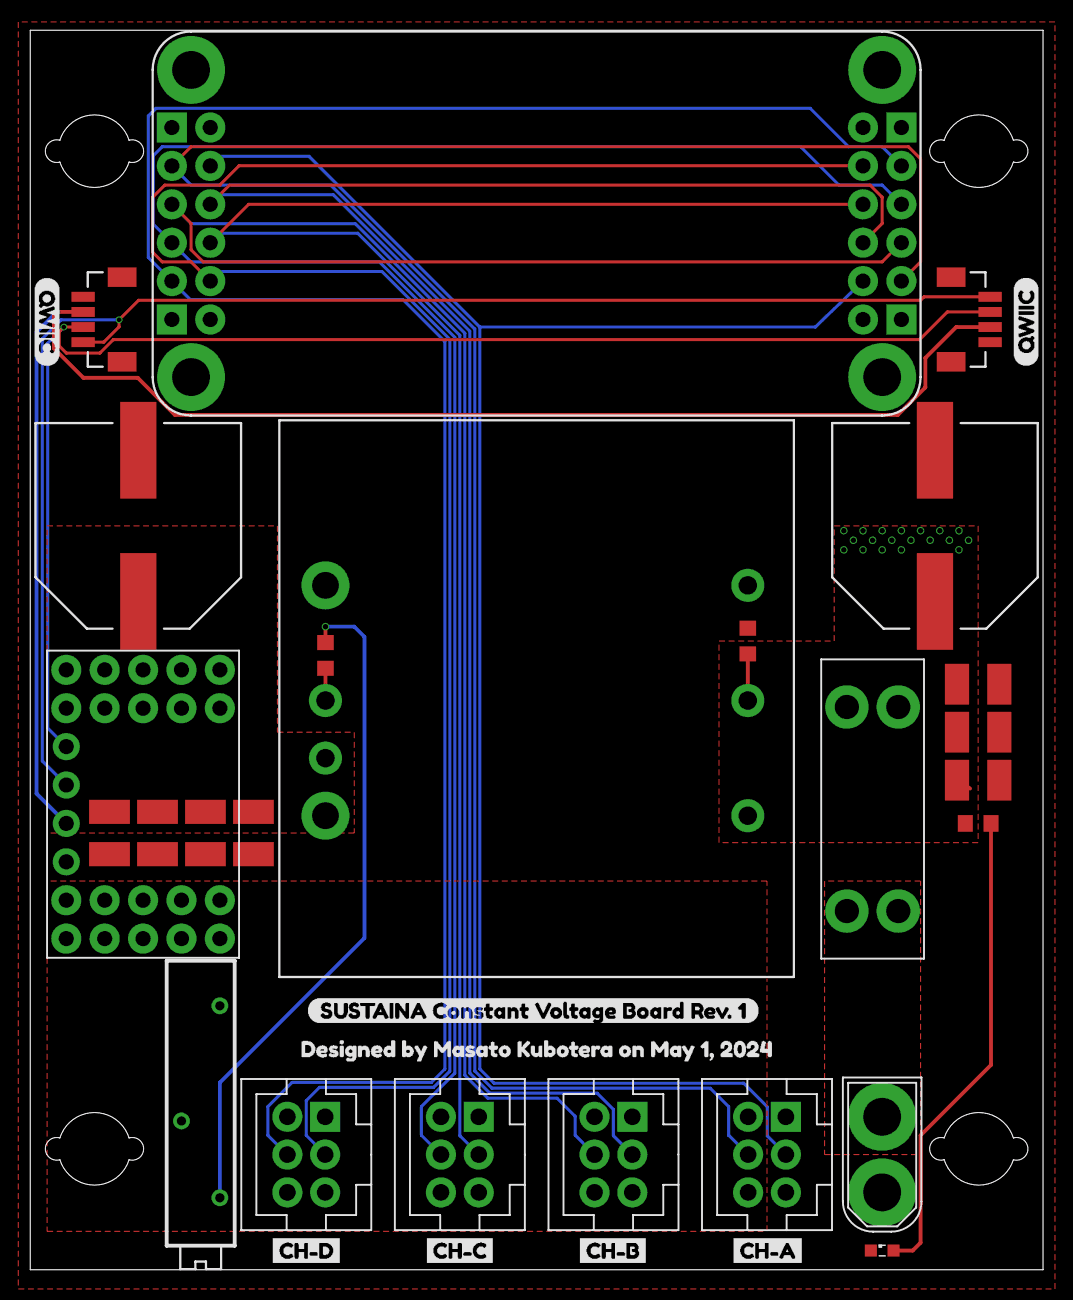
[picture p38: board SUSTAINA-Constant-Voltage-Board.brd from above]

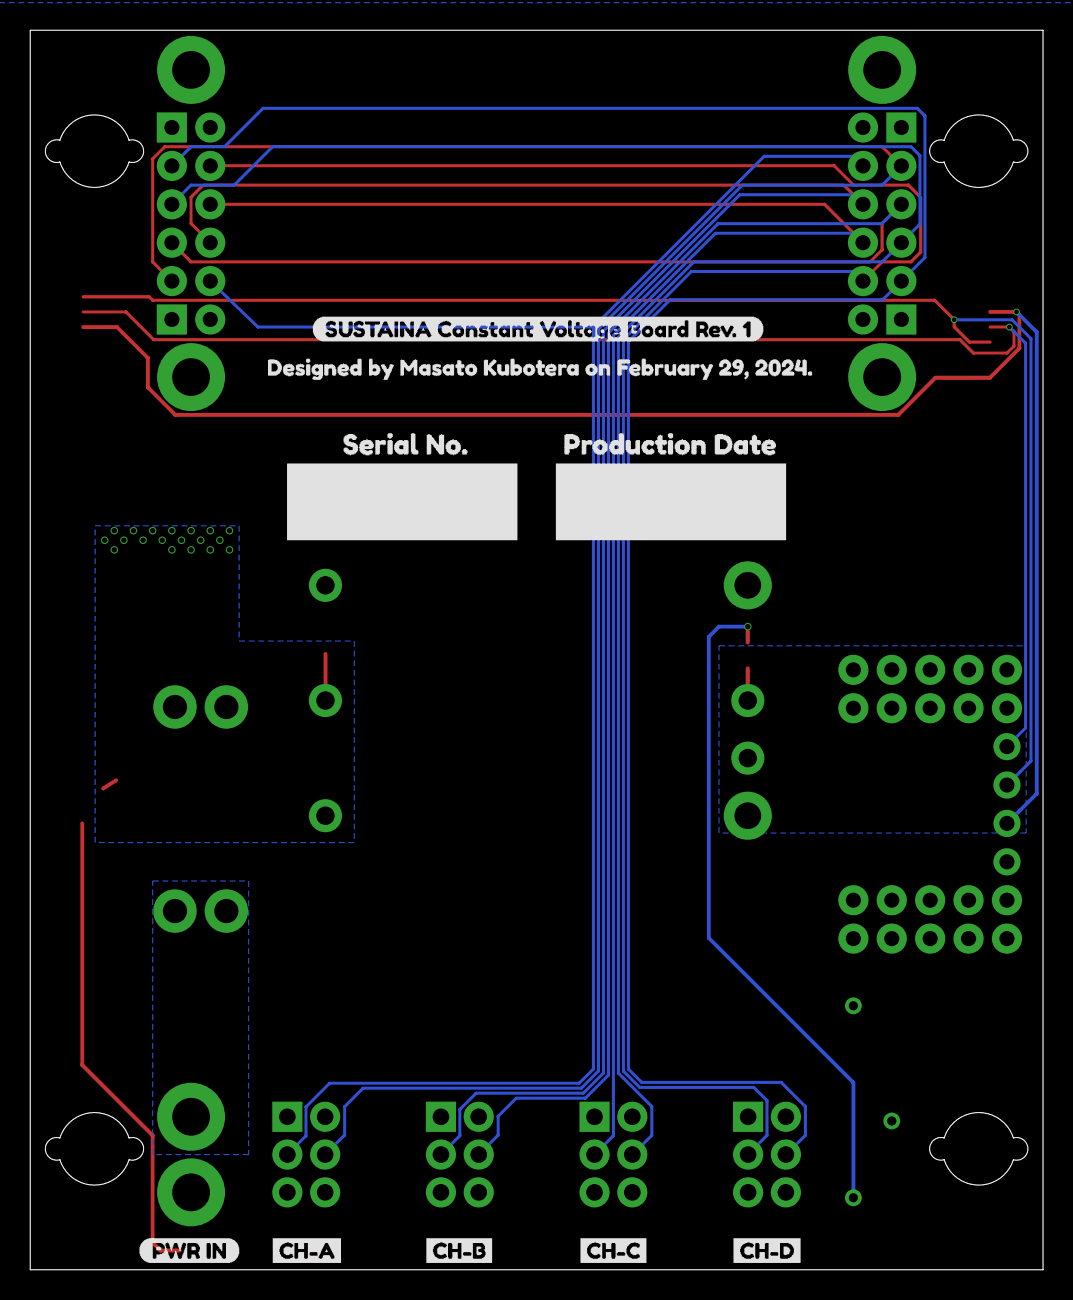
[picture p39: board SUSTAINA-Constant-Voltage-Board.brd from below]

Board: 2 copper layers, 67.0 x 82.0 mm, 42 parts (9 on the bottom side), 20 nets.

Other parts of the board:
U$1, U$18: CONSTANT_VOLTAGE_REV#_10; SUSTAINA_CONSTANT_VOLTAGE_BOARD_REV#_1
U$2: DESIGNED_BY_MASATO_KUBOTERA_ON_FEBRUARY_190DESIGN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; DESIGNED_BY_MASATO_KUBOTERA_ON_FEBRUARY_290
U$3: PRODUCTION_DATE0
U$4: SERIAL_NO#0
U$6, U$7: QWIIC0
U$8, U$12: CH#A1
U$9, U$13: CH#B1
U$10, U$14: CH#C1
U$11, U$15: CH#D1
U$16: PWR_IN0
U$17: DESIGNED_BY_MASATO_KUBOTERA_ON_MAY_1

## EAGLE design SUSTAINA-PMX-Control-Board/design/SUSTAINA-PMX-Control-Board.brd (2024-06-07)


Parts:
C1: 0.1u; C0603
C2: 10u; C0603
CH1: XT30U-M
CH2, CH3, CH4, CH5: DF1BZ-6DP-25DSA
CH6, CH7, CH8, CH9: B2B-PH-K-S(LF)(SN)
LED1: Green; SML0603
M1: USB-TO-QUAD-RS-485-CONV-MODULESINGLE; USB-TO-QUAD-RS-485-CONV-MODULE-TPLACE-SINGLE
R1: 2k; R0603
U1: LM2937IMP-12NOPB; SOT-223

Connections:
+12V: C2.1, CH6.2, CH7.2, CH8.2, CH9.2, U1.3 (VOUT)
+PWR: C1.1, CH1.+, CH2.2, CH2.6, CH3.2, CH3.6, CH4.2, CH4.6, CH5.2, CH5.6, R1.2, U1.1 (VIN)
A-DM: CH2.4, M1.A-RS-485-DM1 (A-RS485-DM)
A-DP: CH2.3, M1.A-RS-485-DP1 (A-RS485-DP)
B-DM: CH3.4, M1.B-RS-485-DM1 (B-RS485-DM)
B-DP: CH3.3, M1.B-RS-485-DP1 (B-RS485-DP)
C-DM: CH4.4, M1.C-RS-485-DM1 (C-RS485-DM)
C-DP: CH4.3, M1.C-RS-485-DP1 (C-RS485-DP)
D-DM: CH5.4, M1.D-RS-485-DM1 (D-RS485-DM)
D-DP: CH5.3, M1.D-RS-485-DP1 (D-RS485-DP)
GND: C1.2, C2.2, CH1.-, CH2.1, CH2.5, CH3.1, CH3.5, CH4.1, CH4.5, CH5.1, CH5.5, CH6.1, CH7.1, CH8.1, CH9.1, LED1.C, M1.GND-1, M1.GND-2, U1.2 (GND)
LED_PWR: LED1.A, R1.1

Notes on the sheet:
June 1, 2024
SUSTAINA PMX Control Board
1.0
1/1
USB / RS485 Conv. Module
PMX Connecters
Constant Voltage
DC Fan
Power Generation



Board: 2 copper layers, 67.0 x 45.0 mm, 30 parts (4 on the bottom side), 12 nets.

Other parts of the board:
U$1, U$2: DESIGNED_BY_MASATO_KUBOTERA_ON_FEBRUARY_190DESIGN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; DESIGNED_BY_MASATO_KUBOTERA_ON_JUNE_1
U$3: PRODUCTION_DATE0
U$4: SERIAL_NO#0
U$5, U$6: PMX
U$7, U$19: DC_FAN
U$8: CH#A1
U$9: CH#B1
U$10: CH#C1
U$11: CH#D1
U$12, U$13: SUSTAINA_PMX_CONTROL_BOARD_REV#_1
U$16: PWR_IN0

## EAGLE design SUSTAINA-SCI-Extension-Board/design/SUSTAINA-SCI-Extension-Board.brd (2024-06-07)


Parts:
CH1, CH2: XF2M-2215-1A

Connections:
unnamed: CH1.22, CH2.1
unnamed: CH1.21, CH2.2
unnamed: CH1.20, CH2.3
unnamed: CH1.19, CH2.4
unnamed: CH1.18, CH2.5
unnamed: CH1.17, CH2.6
unnamed: CH1.16, CH2.7
unnamed: CH1.15, CH2.8
unnamed: CH1.14, CH2.9
unnamed: CH1.13, CH2.10
unnamed: CH1.12, CH2.11
unnamed: CH1.11, CH2.12
unnamed: CH1.10, CH2.13
unnamed: CH1.9, CH2.14
unnamed: CH1.8, CH2.15
unnamed: CH1.7, CH2.16
unnamed: CH1.6, CH2.17
unnamed: CH1.5, CH2.18
unnamed: CH1.4, CH2.19
unnamed: CH1.2, CH2.21
unnamed: CH1.3, CH2.20
unnamed: CH1.1, CH2.22

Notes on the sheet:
June 1, 2024
SUSTAINA SCI Extension Board
1.0
1/1
SCI Connecters


Board: 2 copper layers, 20.0 x 17.5 mm, 4 parts (2 on the bottom side), 22 nets.

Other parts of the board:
U$1: SUSTAINA_SCI_EXTENSION_BOARD-0.03
U$2: DESIGNED_BY_MASATO_KUBOTERA_ON_JUNE_1-0.03

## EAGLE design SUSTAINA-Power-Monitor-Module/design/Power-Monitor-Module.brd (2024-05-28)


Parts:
C1, C2: 0.1u; C0402
IC1: INA226; MSOP-10
JP1, JP2, JP3, JP4, JP5, JP6, JP7, JP8: SHORTLAND
LED1: Red; SML0603
LED2: Yellow; SML0603
P1, P2: 2X5P
P3: 1X4P
R1: 0.002; R2512
R2, R3: 4.7; R0402
R4, R5: 2k; R0402

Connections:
A0: IC1.2 (A0), JP1.1, JP2.1, JP3.1, JP4.1
A1: IC1.1 (A1), JP5.1, JP6.1, JP7.1, JP8.1
ALERT: IC1.3 (ALERT)
GND: C2.2, IC1.7 (GND), JP1.2, JP5.2, LED1.C, LED2.C, P3.1
IN+: C1.1, IC1.8 (VBUS), IC1.10 (IN+), R2.2
IN-: C1.2, IC1.9 (IN-), R3.2
LED1_: LED1.A, R4.1
LED2: LED2.A, R5.1
SCL: IC1.5 (SCL), JP4.2, JP8.2, P3.3
SDA: IC1.4 (SDA), JP3.2, JP7.2, P3.4
VIN+: P1.1, P1.2, P1.3, P1.4, P1.5, P1.6, P1.7, P1.8, P1.9, P1.10, R1.2, R2.1
VIN-: P2.1, P2.2, P2.3, P2.4, P2.5, P2.6, P2.7, P2.8, P2.9, P2.10, R1.1, R3.1, R4.2
VS: C2.1, IC1.6 (VS), JP2.2, JP6.2, P3.2, R5.2

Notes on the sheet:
I2C Address Selection by Shortland
Pinhedders
Current-shunt and power monitor
May 25, 2024
SUSTAINA Power Monitor Module
3.0
1/1
Address Pins and Slave Addresses A1 | A0 | SLAVE ADDRESS GND | GND | 1000000 (0x64) GND | VS | 1000001 (0x65) GND | SDA | 1000010 (0x66) GND | SCL | 1000011 (0x67) VS | GND | 1000100 (0x68) VS | VS | 1000101 (0x69) VS | SDA | 1000110 (0x70) VS | SCL | 1000111 (0x71) SDA | GND | 1001000 (0x72) SDA |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
Indicators



Board: 2 copper layers, 20.3 x 12.7 mm, 25 parts (4 on the bottom side), 12 nets.

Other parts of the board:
U$1, U$2: POWER_MONITOR_MODULE
U$3: REV#_3
U$5: DESIGNED_BY_MASATO_KUBOTERA_ON_MAY_25-0.0225

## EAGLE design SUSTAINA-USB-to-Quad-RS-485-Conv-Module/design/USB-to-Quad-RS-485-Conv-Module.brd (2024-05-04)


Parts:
C1, C3: 0.01u; C0402
C2: 1u; C0402
C4: 2.2u; C0402
C5, C7, C16: 4.7u; 0805K
C6, C8, C9, C10, C11, C12, C13, C14, C15, C17, C18, C21, C22, C23, C24, C25: 0.1u; C0402
C19, C20: 30p; C0402
CR1: 7V12006001
D1, D2: PGB1010603MR; 0603
D3, D4, D5, D6: CDSOT23-SM712; SOT-23-3
FL1, FL2, FL3: BLM15AX601SN1D
IC1: FT4232HQ
IC2: 93LC56BT-I/OT; SOT-23-6
IC3, IC4, IC5, IC6: SN65HVD75DRBR; SON65P300X300X100-9N
IC7: SN74HC595B; QFN40P250X250X50-17N
LED1, LED2, LED8, LED10, LED12, LED14: Green; SML0603
LED7, LED9, LED11, LED13: Red; SML0603
M1: USB-TO-QUAD-RS-485-CONV-MODULEDIMENSION; USB-TO-QUAD-RS-485-CONV-MODULE-DIMENSION
R1, R2, R22, R23, R24, R25, R26, R27, R28, R29: 470; R0402
R3, R4: 10; R0402
R5: 15k; R0402
R6, R8, R30: 10k; R0402
R7: 12k; R0402
R9: 2k; R0402
R10, R12, R13, R15, R16, R18, R19, R21: 680; R0402
R11, R14, R17, R20: 120; R0402
U1: TPS73533DRBT; SON-8
USB1: USB-C-2.0

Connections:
+1V8: C13.1, C14.1, C15.1, C16.1 (+), C17.1, IC1.12 (VCORE), IC1.37 (VCORE), IC1.49 (VREGOUT), IC1.64 (VCORE)
+3V3: C4.1, C9.1, C10.1, C11.1, C12.1, C18.1, C21.1, C22.1, C23.1, C24.1, C25.1, FL2.1, FL3.1, IC1.20 (VCCIO), IC1.31 (VCCIO), IC1.42 (VCCIO), IC1.50 (VREGIN), IC1.56 (VCCIO), IC2.6 (VCC), IC3.8 (VCC), IC4.8 (VCC), IC5.8 (VCC), IC6.8 (VCC), IC7.10 (!SRCLR), IC7.16 (VCC), M1.3V3-1, M1.3V3-2, R2.2, R8.1, R10.2, R13.2, R16.2, R19.2, R30.2, U1.1 (OUT)
+5V: C2.1, FL1.2, R1.2, R5.1, U1.5 (EN), U1.8 (IN)
A-DM: D3.1, IC3.7 (B), M1.A-RS-485-DM (A-RS485-DM), R11.1, R12.2
A-DP: D3.2, IC3.6 (A), M1.A-RS-485-DP (A-RS485-DP), R10.1, R11.2
A-RX: IC7.1 (QB), R23.2
A-RXD: IC1.17 (ADBUS1), IC3.1 (R)
A-TX: IC7.15 (QA), R22.2
A-TXD: IC1.16 (ADBUS0), IC3.4 (D)
A-TXDEN: IC1.24 (ADBUS7), IC3.2 (!RE), IC3.3 (DE)
B-DM: D4.1, IC4.7 (B), M1.B-RS-485-DM (B-RS485-DM), R14.1, R15.2
B-DP: D4.2, IC4.6 (A), M1.B-RS-485-DP (B-RS485-DP), R13.1, R14.2
B-RX: IC7.3 (QD), R25.2
B-RXD: IC1.27 (BDBUS1), IC4.1 (R)
B-TX: IC7.2 (QC), R24.2
B-TXD: IC1.26 (BDBUS0), IC4.4 (D)
B-TXDEN: IC1.34 (BDBUS7), IC4.2 (!RE), IC4.3 (DE)
C-DM: D5.1, IC5.7 (B), M1.C-RS-485-DM (C-RS485-DM), R17.1, R18.2
C-DP: D5.2, IC5.6 (A), M1.C-RS-485-DP (C-RS485-DP), R16.1, R17.2
C-RX: IC7.5 (QF), R27.2
C-RXD: IC1.39 (CDBUS1), IC5.1 (R)
C-TX: IC7.4 (QE), R26.2
C-TXD: IC1.38 (CDBUS0), IC5.4 (D)
C-TXDEN: IC1.46 (CDBUS7), IC5.2 (!RE), IC5.3 (DE)
CLK: IC1.62 (EECLK), IC2.4 (CLK), IC7.11 (SRCLK)
CS: IC1.63 (EECS), IC2.5 (CS), IC7.12 (RCLK)
D-DM: D6.1, IC6.7 (B), M1.D-RS-485-DM (D-RS485-DM), R20.1, R21.2
D-DP: D6.2, IC6.6 (A), M1.D-RS-485-DP (D-RS485-DP), R19.1, R20.2
D-RX: IC7.7 (QH), R29.2
D-RXD: IC1.52 (DDBUS1), IC6.1 (R)
D-TX: IC7.6 (QG), R28.2
D-TXD: IC1.48 (DDBUS0), IC6.4 (D)
D-TXDEN: IC1.59 (DDBUS7), IC6.2 (!RE), IC6.3 (DE)
DATA: IC1.61 (EEDATA), IC2.3 (DI), IC7.14 (SER), R9.2
FT4232H-DM: IC1.7 (DM), R3.2
FT4232H-DP: IC1.8 (DP), R4.2
FT4232H-REF: IC1.6 (REF), R7.2
GND: C1.2, C2.2, C3.2, C4.2, C5.2 (-), C6.2, C7.2 (-), C8.2, C9.2, C10.2, C11.2, C12.2, C13.2, C14.2, C15.2, C16.2 (-), C17.2, C18.2, C19.2, C20.2, C21.2, C22.2, C23.2, C24.2, C25.2, CR1.2, CR1.4, D1.1, D2.1, D3.3, D4.3, D5.3, D6.3, IC1.1 (GND), IC1.5 (GND), IC1.10 (AGND), IC1.11 (GND), IC1.13 (TEST), IC1.15 (GND), IC1.25 (GND), IC1.35 (GND), IC1.47 (GND), IC1.51 (GND), IC2.2 (GND), IC3.5 (GND), IC4.5 (GND), IC5.5 (GND), IC6.5 (GND), IC7.8 (GND), IC7.17 (EP), LED1.C, LED2.C, LED7.C, LED8.C, LED9.C, LED10.C, LED11.C, LED12.C, LED13.C, LED14.C, M1.GND-1, M1.GND-2, R6.1, R7.1, R12.1, R15.1, R18.1, R21.1, U1.2 (GND), U1.4 (GND), U1.6 (GND), U1.7 (GND), U1.9 (GND), U1.10 (GND), U1.11 (GND), U1.12 (GND), U1.13 (GND), USB1.GND, USB1.GND2 (GND), USB1.SHLD1 (SHLD), USB1.SHLD2 (SHLD), USB1.SHLD3 (SHLD), USB1.SHLD4 (SHLD), USB1.SHLD5 (SHLD), USB1.SHLD6 (SHLD), USB1.SHLD7 (SHLD), USB1.SHLD8 (SHLD)
LED-A-RX: LED8.A, R23.1
LED-A-TX: LED7.A, R22.1
LED-B-RX: LED10.A, R25.1
LED-B-TX: LED9.A, R24.1
LED-C-RX: LED12.A, R27.1
LED-C-TX: LED11.A, R26.1
LED-D-RX: LED14.A, R29.1
LED-D-TX: LED13.A, R28.1
LED_3V3: LED2.A, R2.1
LED_5V: LED1.A, R1.1
NR/FB: C3.1, U1.3 (NR/FB)
OSCI: C19.1, CR1.1, IC1.2 (OSCI)
OSCO: C20.1, CR1.3, IC1.3 (OSCO)
PULLUP-DATA: IC2.1 (DO), R8.2, R9.1
PWREN: IC1.60 (PWREN#), IC7.13 (!OE), R30.1
RESET: IC1.14 (RESET#), R5.2, R6.2
USB-DM: D1.2, R3.1, USB1.A7 (D-), USB1.B7 (D-)
USB-DP: D2.2, R4.1, USB1.A6 (D+), USB1.B6 (D+)
VBUS: C1.1, FL1.1, USB1.VBUS1 (VBUS), USB1.VBUS2 (VBUS)
VPHY: C5.1 (+), C6.1, FL2.2, IC1.4 (VPHY)
VPLL: C7.1 (+), C8.1, FL3.2, IC1.9 (VPLL)

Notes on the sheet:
USB to UART Conv.
UART to RS-485 Conv.
CH-A
CH-D
CH-C
CH-B
Transmission Line Terminating Resistors
Module Pinheader Holes
Status LEDs ( Optional )
LC Filtering
5V to 3.3V Voltage Con. ( Optional )
USB 2.0 Mini-B input port ( Optional )
2.0
1/1
May 1, 2024
SUSTAINA- USB to RS-485 Conv. Module
LED Indicator



Board: 2 copper layers, 50.8 x 25.4 mm, 117 parts (4 on the bottom side), 59 nets.

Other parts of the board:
U$1: DESIGNED_BY_MASATO_KUBOTERA_ON_MAY_1-COLUMN
U$3: CH#A0
U$4: CH#B0
U$5: CH#C0
U$6: CH#D0
U$7: D-DM-0.025
U$8: D-DP-0.025
U$9: USB#QUAD_RS#485_REV#_2
U$11, U$13, U$15, U$17: RX0
U$12, U$14, U$16, U$18: TX0
U$23, U$24, U$31: 3V3_0.025
U$25, U$26: GND_0.025
U$27: USB_TO_QUAD_RS#485_CONV#_MODULE_REV#_20; SUSTAINA_USB_TO_QUAD_RS#485_CONV#_MODULE_REV#_2
U$28: A-DM-0.025
U$29: PRODUCTION_DATE0
U$30: SERIAL_NO#0
U$32: C-DP-0.025
U$33: DESIGNED_BY_MASATO_KUBOTERA_ON_MAY_1
U$34: A-DP-0.025
U$35: C-DM-0.025
U$36: B-DP-0.025
U$37: B-DM-0.025
U$38: VBUS_0.025

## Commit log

2024-05-02 add PCBs for SUSTAINA-OP2
    [Power-Monitor-Module-Panel.brd, Power-Monitor-Module-Panel.sch, Power-Monitor-Module-Panel_bom.csv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]
2024-05-03 deleted the imposition file due to unavailability of the order
    [Power-Monitor-Module-Panel.brd, Power-Monitor-Module-Panel.sch]
2024-05-04 Added connector for DC fans to SUSTAINA-Constant-Voltage-Board
    [SUSTAINA-Constant-Voltage-Board.brd, SUSTAINA-Constant-Voltage-Board.sch, SUSTAINA-Constant-Voltage-Board_top_bom.csv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]
2024-05-28 Corrected the silk printing and via processing method
    [Power-Monitor-Module.brd, Power-Monitor-Module.sch, Power-Monitor-Module_bom.csv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]
2024-06-07 Add mass-produced version of Control-Switches-Board
    [SUTAINA-Control-Switches-Board.brd, SUTAINA-Control-Switches-Board.sch, SUTAINA-Control-Switches-Board_bom.csv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]
2024-06-07 Add mass-produced version of SCI-Extension-Board
    [SUSTAINA-SCI-Extension-Board.brd, SUSTAINA-SCI-Extension-Board.sch, SUSTAINA-SCI-Extension-Board_bom.csv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]
2024-06-07 Add mass-produced version of PMX-Control-Board
    [SUSTAINA-PMX-Control-Board.brd, SUSTAINA-PMX-Control-Board.sch, SUSTAINA-PMX-Control-Board_bom.csv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]
2024-06-07 Add mass-produced version of Power-Distribution-Board
2024-06-07 Add Power-Logging-Board documentation files
2024-06-07 Add mass-produced version of SBC-Power-Board
    [SUSTAINA-SBC-Power-Board_top_bom.csv]
2024-06-07 Add StrainGauge-Sensing-Board documentation files
2024-06-07 add pcba image of Power-Monitor-Module
2024-06-07 Revert Constant-Voltage-Board to version without fan connectors and add data and documentation for outsourcing
    [SUSTAINA-Constant-Voltage-Board.brd, SUSTAINA-Constant-Voltage-Board.sch, SUSTAINA-Constant-Voltage-Board_bom.csv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]
2024-06-11 Add mass-produced version of Power-Supply-Switching-Board
    [SUSTAINA-Power-Supply-Switching-Board.brd, SUSTAINA-Power-Supply-Switching-Board.sch, SUSTAINA-Power-Supply-Switching-Board_bom.csv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]
2024-06-12 Corrected file paths
    [SUSTAINA-Control-Switches-Board.brd, SUSTAINA-Control-Switches-Board.sch, SUTAINA-Control-Switches-Board_bom.csv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]
2024-06-18 Corrected a via error and added some capacitors
    [SUSTAINA-Power-Supply-Switching-Board.brd, SUSTAINA-Power-Supply-Switching-Board.sch, SUSTAINA-Power-Supply-Switching-Board_bom.csv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]
2024-06-24 Add audio borad
    [SUSTAINA-Audio-Board.brd, SUSTAINA-Audio-Board.sch, SUSTAINA-Audio-Board_bom.csv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]

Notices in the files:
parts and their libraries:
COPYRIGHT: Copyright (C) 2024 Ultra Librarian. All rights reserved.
